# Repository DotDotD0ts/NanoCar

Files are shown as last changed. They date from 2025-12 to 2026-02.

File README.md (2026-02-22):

# NanoCar

Projet pour l'option prototypage de mon école. Je veux créer un petit véhicule électrique (style voiture radiocommandé) avec une carte jetson nano et une caméra pi dans le but de faire de la reconnaissance d'objet pour suivre une cible. La jetson hostera aussi un serveur web contenant un retour caméra ainsi que des controles pour le véhicule.
Le prototype sera développé en Python pour un dévelopement rapide et fonctionnel. 

## To do list

**Management**
- [x] Définition du besoin
- [x] Création du cahier des charges
    - [x] Analyse fonctionnelle
    - [x] Planning prévisionnel
    - [x] Diagramme fast
- [x] Commande du matériel
- [x] WBS (a mettre au propre)
- [x] Mise en place du Gantt
- [x] Budget (a mettre au propre)

**Réalisation physique**
- [x] Réflexion sur la partie direction du véhicule (une bille a l'avant et direction avec un differentiel de rotation dans les roues arrieres)
- [x] Conception 3D
    - [x] Jetson nano
    - [x] LiPo
    - [x] Moteur
    - [x] Driver
    - [x] Camera
    - [x] Regulateur
    - [x] Roue
    - [x] Chassis
    - [x] Roue avant
    - [x] Supports pour l'assemblage
        - [x] Batterie
        - [x] Moteurs
        - [x] Caméra
    - [x] Persage des trous de vis (fixation composants)
    - [x] Assemblage 3D
- [x] Fabrication
- [x] Assemblage
- [x] Branchements

**Réalisation logiciel**
- [x] Setup du wifi de la Jetson Nano (10.42.0.1:3000)
- [x] Ajout d'une connexion ssh pour un accès simple à la Jetson Nano
- [x] Mise en place d'un serveur sur la jetson nano
    - [x] Serveur flask
    - [x] Implémentation des commandes
- [x] Création de l'interface utilisateur
- [x] Mise en place du flux vidéo
- [x] Controle des moteurs
- [x] Control manuel du véhicule
    - [x] Différentiel des moteurs pour la direction
    - [x] Paramétrage de l'accéleration / décéleration
- [x] Intégration d'un modèle open source de reconnaissance d'objet
    - [x] Haar Cascade : reconnaissance de visage (CPU only) très lent, latence de plusieurs secondes + 2-3 FPS max
    - [x] SSD Mobilenet v2 : https://github.com/dusty-nv/jetson-inference, detecte le corps humain (GPU accelerated) latence 1-2 secondes, 60 FPS
- [x] Control autonome du véhicule
- [x] Mode recherche de cible si aucune cible dans le visuel (Ajout d'un boulean pour activer ou non)
- [x] Démarage automatique du serveur (crontab)
- [x] Esquive d'obstacles

**Problèmes**
- [x] Méthode Haar Cascade pour reconaissance de visage trop lente (2-3 fps)
- [x] Support caméra n'a pas d'angle, les visages ne sont reconnu que s'ils sont au niveau du sol

**User experience**
- [x] Syncroniser le slider de speed avec le backend
- [x] Réduire la taille de la cible pour que le robot reste plus loin

**Livrable**
- [x] Création d'un poster de présentation du projet
- [x] Rédaction d'une documentation utilisateur 
- [x] Rédaction d'une documentation technique permettant de refaire le projet de zéro

## Documentations

Cette documentation a été réalisé sur l'outil fabmanager comme demandé par l'école. Pour voir le rendu correct de cette doc, veillez-vous rendre sur [ce lien](https://cesi-fabmanager.duckdns.org/#!/projects/nanocar)

# NanoCar

Illustration

La robotique autonome est le domaine consistant à concevoir  
des systèmes capables d'interagir avec leur environnement. Il  
s’agit d’un point clé avec énormément d’enjeux pour l’industrie  
et la mobilité de demain. L’intelligence artificielle, prenant de  
plus en plus d’importance, permet désormais d'intégrer de la  
vision par ordinateur complexe sur de petits systèmes  
embarqués. C’est pour cela que je vous présente mon robot  
autonome Nanocar. Il a pour but de suivre une personne sans  
intervention extérieur.

Vous pouvez retrouver l’entièreté des fichiers concernant ce projet dans le repo&nbsp;[Github NanoCar](https://github.com/DotDotD0ts/NanoCar)

## Étapes

### Étape 1 : Documentation utilisateur

Dans un premier temps, voici la documentation utilisateur qui vous permettra d'utiliser ce prototype :

1. Branchez la batterie LiPo au connecteur jaune sur le côté du robot. Ce connecteur permet d'alimenter l'entièreté du robot.
2. Vérifiez que la LED du driver clignote en bleu sinon chargez la batterie, cette LED indique que la LiPo est suffisamment chargé pour ne pas perdre en durée de vie. (Le driver est la carte électronique brancher directement à la batterie par le connecteur jaune)
3. Utilisez un appareil pour vous connecter au réseau Wifi NanoCar.
4. Ouvrez un navigateur internet et connectez-vous à l'adresse [http://10.42.0.1:3000/](http://10.42.0.1:3000/.)&nbsp;. Cela vous permettra d'avoir l'accès à la page de contrôle du robot.

Utilisation du robot à partir de la page de contrôle :

- Utilisez les flèches directionnelles sur l'écran de contrôle ou sur votre clavier pour faire bouger le robot. (La touche espace permet de freiner)
- Changez la vitesse du robot à l'aide du slider en dessous des boutons.
- Le bouton MODE permet de changer entre les 2 modes du robot : le mode manuel (par défaut) où vous contrôlez le robot à l'aide de l'interface et le mode automatique où une IA va prendre le contrôle du robot est va essayer de suivre une personne. Dans le mode automatique, vous remarquerez que le retour caméra affiche des informations sur ce que l'IA reconnais.&nbsp;
- Le bouton SEARCH permet, en mode automatique, au robot de chercher sa cible au lieu d'attendre qu'elle passe dans son champ de vision.

Enfin pour éteindre le robot il suffit de débrancher le connecteur jaune de la batterie.



### Étape 2 : La liste de course

Pour ce projet, j'ai réutilisé un maximum de composants d'autres projets du Fablab, vous n'êtes en aucun cas obligé de réutiliser les mêmes références. La seul nécessité est que le driver des moteurs accepte une communication série bien particulière. Il reste possible d'adapter le code pour la communication entre la Jetson Nano et le driver.

Voici les composants / matériaux utilisés :

- Une planche de bois de 6mm d'épaisseur.
- 42g de PLA.
- Une multitude de petit câble mâle vers mâle et femelle vers mâle.
- Une multitude de vis et d'écrou m2 et m3
- 2 roues avec une vis permettant de sécuriser la roue à l'axe du moteur.
- 1 ball caster pour la roue avant.
- 2 moteurs DC. Ici des&nbsp;[313 RPM HD Premium Planetary Gear Motor w/Encoder](https://www.servocity.com/313-rpm-hd-premium-planetary-gear-motor-w-encoder/). Ils sont beaucoup trop puissant par rapport aux attentes du prototype.
- Un driver pour contrôler les moteurs. Ici une Sabertooth 2x25. De même pas besoin d'un contrôleur aussi poussé. Si vous ne souhaitez pas toucher au code, il vous faudra un driver qui peut être contrôlé par une communication série de la même façon que la Sabertooth. (Vérifiez que la partie simplified serial de la documentation de votre driver corresponde à la&nbsp;[documentation Sabertooth](https://www.dimensionengineering.com/datasheets/Sabertooth2x25.pdf)). Sinon vous pouvez toujours adapter le fichier command.py pour que la communication corresponde à votre driver.
- Une Jetson Nano (le cerveau du robot qui permet de faire tourner un modèle de reconnaissance d'objet).
- Une carte micro SD de 32Go.
- Une caméra Pi camera v2.1. Dans le cas où vous voulez en utiliser une autre il faudra modifier l'initialisation de la caméra dans le fichier camera.py pour que la librairie OpenCV puisse récupérer l'image.
- Un&nbsp;[dongle Wifi](https://www.amazon.fr/Cudy-Adaptateur-WU300-Hotspot-compatible/dp/B0FR443YP5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) qui fait Access point et qui fonctionne sur Linux. Vérifiez bien les 2 mentions à l'achat.
- Une batterie LiPo 4S.
- Un connecteur XT60 femelle pour connecter le driver à la LiPo.
- Un régulateur de courant pour faire descendre le 14V de la batterie en 5V pour l'alimentation de la Jetson Nano.
- Un cable d'alimentation 5V 4A pour alimenter la Jetson Nano.
- Dans le cas où votre driver est contrôlé par du 5V comme sur la Sabertooth, il vous faudra un level shifter 3V vers 5V pour éviter de cramer la Jetson Nano. Il est nécessaire de protéger la Jetson Nano qui ne prend que du 3V sur les pins I/O.

### Étape 3 : Préparation de la Jetson Nano

Maintenant que nous avons tous les composants, commençons la réalisation.

Brancher le dongle Wifi sur la Jetson Nano ainsi que la carte micro SD et la caméra.

Dans un premier temps, il vous faudra installer l'OS sur la Jetson Nano. Pour cela, je vous laisse suivre le guide fourni par Nvidia : [https://developer.nvidia.com/embedded/learn/get-started-jetson-nano-devkit](https://developer.nvidia.com/embedded/learn/get-started-jetson-nano-devkit). Je vous conseille de définir le nom d'utilisateur en tant que 'nano' vu que c'est celui qui sera utiliser pour le reste de la documentation.

Pour la suite, il va être important d'être connecter à internet. Pour cela, utilisez l'utilitaire graphique d'Ubuntu en haut à droite de l'écran ou nmtui si vous utilisez une connexion serial ou ssh à la carte.

Une fois connecté à un réseau Wifi ayant un accès internet, à l'aide d'un terminal, exécuter les commandes suivantes :

Mettre en place le DNS :

    sudo echo "nameserver 8.8.8.8" > /etc/resolv.conf
    sudo systemctl restart NetworkManager

Installer les dépendances :

    sudo apt-get update
    sudo apt-get install python3-pip cmake git  
    pip3 install flask libpython3-dev python3-numpy

Pour préparer git pour récupérer le code source du projet ainsi que celui des dépendances. Vous pouvez mettre ce que vous souhaitez en nom utilisateur et email :&nbsp;

    git config --global user.name "[votre nom d'utilisateur]"
    git config --global user.email "[votre email]"

Installer Jetson Inference est nécessaire pour la partie reconnaissance d'objet du projet :

    sudo apt-get install git cmake libpython3-dev python3-numpy
    git clone --recursive --depth=1 https://github.com/dusty-nv/jetson-inference
    cd jetson-inference
    mkdir build
    cd build
    cmake ../
    make -j$(nproc)
    sudo make install
    sudo ldconfig

Voici le lien de la documentation d'où viennent les commandes : [https://github.com/dusty-nv/jetson-inference/blob/master/docs/building-repo-2.md](https://github.com/dusty-nv/jetson-inference/blob/master/docs/building-repo-2.md).

Ensuite, copier le répertoire Github de NanoCar avec la commande :

    git clone[https://github.com/DotDotD0ts/NanoCar.git](https://github.com/DotDotD0ts/NanoCar.git)

Enfin, pour que le code se lance à chaque démarrage, nous allons configurer l'utilitaire linux crontab :

    sudo crontab -e

Cette commande va vous ouvrir un fichier dans lequel il va falloir mettre la ligne suivante :&nbsp;

    @reboot python3 /home/nano/NanoCar/src/main.py

Sauvegardez le fichier avec Ctrl + o puis fermez le avec Ctrl + x.

Maintenant, plus besoin de connexion internet, nous pouvons préparer la carte à créer son propre réseau Wifi pour si connecter.

Pour cela, ouvrez un terminal puis entrez les commandes suivantes :

    # 1. Création de la connexion et du nom du réseau (SSID = NanoCar)sudo nmcli con addtypewifi ifname wlan0 con-name NanoCar autoconnect yes ssid NanoCar# 2. Force le mode Point d'Accèssudo nmcli con modify NanoCar 802-11-wireless.mode ap# 4. Configuration IP (Serveur DHCP)sudo nmcli con modify NanoCar ipv4.method shared# 5. Force la bande 2.4GHz (Plus stable)sudo nmcli con modify NanoCar 802-11-wireless.bandbg  
      
    # 6. Rendre l'adresse IP statique  
    sudo nmcli con modify NanoCarHotspot ipv4.addresses 10.42.0.1/24
      
    # 7. Activer l'interface  
    sudo nmcli con up NanoCar

Maintenant, il est possible de se connecter à la carte avec un ordinateur. Pour cela, connectez l'ordinateur au réseau Wifi NanoCar puis ouvrez un terminal et connectez-vous en SSH :

    ssh nano@10.42.0.1

Le mot de passe du compte utilisateur vous sera demandé.

Cette connexion SSH vous permettra de faire des modifications au code source en cas de besoin.

### Étape 4 : Fabrication

Prenez votre planche en bois, une découpeuse laser et utilisez le CAD du châssis (retrouvable sur le Github dans le dossier CAD) ou le pdf pour découper le châssis dans la planche en bois. Vous pouvez aussi graver les emplacements des différents composants pour rendre l'assemblage plus simple.

Imprimez les supports en PLA à partir des modèles 3D. (vous retrouverez aussi les CAD dans le Github).

Prenez un crayons fin et long puis placez les différents composants, supports imprimés et le ball caster sur la planche en bois. Vous pouvez ainsi marquer les trous à faire pour les vis. Pour placer les composants, référez-vous au CAD NanoCar assemblage ou à l'image de la réalisation finale.

Avec votre châssis marqué, utilisez la perceuse à colonne pour faire des trous de 2 et 3 mm de diamètre. L'image ci-dessus vous permettra de savoir quelles trous doivent être de quelle diamètre.

Il va falloir régler le régulateur de courant, pour cela équipez-vous d'un petit tournevis plat, d'une alimentation 14V (vous pouvez utilisez la batterie directement) et d'un multimètre. Branchez l'alimentation au borne IN + et - du régulateur, réglez votre multimètre en mode voltmètre 20V en courant continu, poser les bornes de votre multimètre sur la sortie OUT + et - puis tourner le potentiomètre bleu à l'aide du tournevis plat jusqu'à ce que vous lisiez 5V sur le multimètre. Cette étape est extrêmement importante pour ne pas griller la Jetson Nano.

Sur la Sabertooth 2x25, vous allez retrouver 6 switchs qui permettent de configurer le driver, je vous laisse lire la&nbsp;[documentation officielle](https://www.dimensionengineering.com/datasheets/Sabertooth2x25.pdf)&nbsp;pour comprendre ce que la configuration suivante fait :&nbsp;

1. ON : Sélection du mode
2. OFF : Sélection du mode
3. ON : Option de protection de la batterie Lithium
4. OFF : Sélection du baud rate
5. ON&nbsp;: Sélection du baud rate
6. ON : Sélection du mode simple serial

Maintenant pour la dernière étape avant l'assemblage final, il va vous falloir souder 6 files sur le level shifter. Du côté LV, il vous faudra des mâles vers femelles et du côté HV il vous faudra des mâles vers mâles.





### Étape 5 : Assemblage

Voici maintenant les étapes de l'assemblage. Vous retrouverez dans les images un schéma électroniques ainsi que toutes les étapes de l'assemblage dans l'ordre.

Vu qu'aucun pas de vis n'est mis en place, nous utiliserons une vis ainsi qu'un écrou pour serrer à chaque fois que j'indique "Vissez".

1. Vissez le régulateur de courant sur le châssis.
2. Connectez le câble d'alimentation 5V pour la Jetson Nano en sortie (le rouge sur le OUT+ et le noir sur le OUT-) et 2 files mâles vers mâles en entrée.
3. Vissez la Jetson Nano.
4. Connectez le driver au level shifter, 5V -\> HV, 0V -\> GND côté HV et le S1 -\> HV1. Vissez le driver.
5. Vissez les supports moteurs sans les serrer puis placer les moteurs. Enfin, serrer les supports pour que les moteurs ne puissent pas bouger. Vissez les supports de la batterie à l'avant.
6. Vissez le support caméra, ne le serré pas trop fort, la batterie viendra aligner la caméra.
7. Branchez le câble d'alimentation 5V à la Jetson Nano. Branchez le connecteur XT60 femelle ainsi que le régulateur de courant au driver, rouge -\> B+ et noir -\> B- ainsi que IN+ -\> B+ et IN- -\> B-. Branchez le level shifer à la JetsonNano, LV -\> 3.3V, GND -\> GND, LV1 -\> pin 8.
8. Branchez les moteurs au driver, Moteur B (à gauche sur l'image) : rouge -\> MB+, noir -\> MB-, Moteur A (à droite sur l'image) : rouge -\> MA+, noir -\> MA-. Vissez les roues sur les moteurs arrière et le ball caster à l'avant.
9. Glissez la batterie dans son emplacement avec le connecteur vers le driver. Enfin, connectez le connecteur jaune XT60 femelle au connecteur de la batterie. Une LED bleu devrait clignoter sur le driver, une LED rouge devrait s'allumer sur le régulateur de courant ainsi que sur la Jetson Nano.

Vous devriez maintenant vous retrouver avec un prototype fonctionnel.





















### Étape 6 : Programmation

Avec ce prototype enfin fonctionnel, il est temps de rentrer dans les détails de la logique. Si vous souhaitez modifier le code source, connectez-vous à l'aide de la connexion SSH comme expliqué à la fin de l'étape 3. Dans le cas où vous n'arrivez pas à vous connecter par le Wifi du robot, il reste possible de brancher directement un câble Ethernet entre le robot et votre PC puis de se connecter en SSH par l'ip de cette connexion.

Pour votre information, les technologies suivantes sont indispensable à ce projet :

- Jetson inference plus précisément SSD-Mobilnet-V2 qui est le modèle d'IA utilisé
- OpenCV une librairie très connu pour son efficacité dans le traitement d'image, ici utilisé pour récupérer le flux vidéo de la caméra
- Flask une libraire permettant de mettre en place très facilement un serveur web
- Enfin, pour la simplicité du langage et la rapidité d'écriture, tout le code est écris en python&nbsp;

Vous retrouverez tous les fichiers dans le dossier src du projet Github.

* * *

**Mise en place du serveur web (voir le fichier main.py)**

Vous pouvez retrouver le point d'entré de ce programme qui lance tout simplement le serveur web.&nbsp;

Dans ce fichier, nous retrouvons aussi la définition des routes du serveur web :

- La route par défaut /, amène sur l'écran de contrôle
- La route /videoFeed, envoie le flux caméra depuis le serveur
- La route /command, permet d'envoyer des commandes au serveur
- La route /currentSpeed, permet la synchronisation de la vitesse entre l'affichage et la vitesse réel du robot&nbsp;

Si vous souhaitez modifier l'écran de contrôle, vous retrouverez le fichier home.html dans le dossier page.

* * *

**Contrôle du véhicule (voir le fichier command.py)**

Dans ce fichier il y a la définition du pin de contrôle de la Jetson Nano avec la variable driverPin, ainsi que l'ouverture de la communication série entre la Jetson et le driver. Le serial port est définit dans la data sheet de la Jetson Nano et le baud rate doit correspondre à la configuration du driver.

La fonction driveMotor permet de transformer une simple vitesse avec un id de moteur en instruction compréhensible par le driver.

Enfin, la fonction execCommand recense toutes les commandes que le serveur peut recevoir et exécute le code permettant d'effectuer cette commande.

* * *

**Un accès simple à des valeurs (voir fichier globalVar.py)**

Pour transmettre facilement une valeur entre des fichiers python, la solution la plus simple reste d'avoir un fichier qui contient les variables à partager en tant que variable globale et d'importer ce fichier.

* * *

**IA et caméra (voir le fichier camera.py)**

Ce fichier rassemble la récupération du flux caméra ainsi que l'exécution de l'IA avec un post traitement pour afficher ce que l'IA a reconnue.

Dans un premier temps, nous ouvrons un chemin entre notre programme est la caméra à l'aide d'OpenCV que l'on va appeler un stream. Cette partie d'initialisation se fait à l'aide d'une chaîne de caractère très particulière qui indique à la Jetson Nano la qualité de l'image, le format de celle-ci ainsi que la fréquence d'image. Ici notre caméra peut se permettre de filmer dans une multitude de qualité dont de la 4k, mais pour notre utilisation, nous préférons la qualité la plus basse soit de la HD mais avec une fréquence d'image bien plus importante. Cela permet à l'IA de prendre beaucoup moins de temps à trouver sa cible et aussi à la suivre de façon plus précise.

Nous retrouvons ensuite l'initialisation du modèle d'IA SSD-Mobilnet-V2 avec un threshold définit ici à 60%. Ce threshold correspond à la confiance du modèle IA dans la reconnaissance d'un objet. Ce paramètre permet de contrôler les faux positifs. Si vous avez beaucoup de faux positif, augmentez le threshold sinon dans le cas contraire où le modèle ne reconnais pas de cible, baisser le.

Puis viennent quelques configuration :

- FRAME\_WIDTH correspond à la largeur du retour caméra définit plus haut.
- DEAD\_ZONE\_X correspond aux nombres de pixels autour du centre qui vont être considéré comme le centre. Cela évite que le robot oscille quand il essaie de pointer vers une cible.
- TARGET\_AREA correspond aux nombres de pixels chercher par le robot pour s’arrêter. Cela va contrôler la distance d'arrêt du robot par rapport à la cible. Si le robot se rapproche trop, réduisez ce nombre, sinon s'il s'éloigne trop, augmentez ce nombre.
- AREA\_TOLERANCE correspond aux nombres de pixels autour de la TARGET\_AREA qui vont être considéré comme la cible. Similairement à la variable DEAD\_ZONE\_X, cela permet d'éviter que le robot oscille d'avant en arrière lorsqu'il est à distance d'arrêt de la cible.&nbsp;&nbsp;

La fonction generateFrames est la fonction qui va permettre au serveur web d'envoyé le flux vidéo à l'écran de contrôle.

Enfin la fonction followTarget permet de passer l'image à l'IA qui nous donne une liste d'objets détectés ainsi que leur position. Nous cherchons dans cette liste la cible définit par globalVar.target\_class\_id (ici 1, si vous souhaitez que la cible soit autre chose qu'un humain, je vous laisse chercher le class id correspondant dans la&nbsp;[documentation du modèle](https://github.com/dusty-nv/jetson-inference/blob/master/data/networks/ssd_coco_labels.txt) est le remplacer). En priorité nous essayons d'esquiver l'obstacle le plus proche s'il est plus proche que la cible. Puis nous allons dans la direction de la cible. Pour finir, nous mettons à jour l'image du flux vidéo en y dessinant un rectangle vert pour la cible et des rectangles rouges pour les obstacles ainsi que leur catégorie

### Étape 7 : Conclusion

Dans l'ensemble, ce prototype est sorti comme imaginer au début du projet. Il correspond au CAD réalisé, toutes les fonctionnalités du cahier des charges sont présentes enfin la réalisation a pris moins de temps que prévu.

Le seul problème rencontré est la remonté d'un courant 5V par l'input S1 du driver dans le pin 8 (3,3V) de la Jetson Nano, ce qui a brulé un composant de celle-ci. Une solution simple a était trouvé rapidement avec l'ajout d'un level shifter.

Malgré un prototype fonctionnel de multiples améliorations sont possibles. Voici une liste non exhaustive d'idées pour améliorer ce prototype :

- Améliorer la logique d'esquive d'obstacles
- Ajouter une sélection de la cible
- Réduire la latence en mode automatique
- Revoir les contrôles du véhicules (par exemple une fonction lerp) pour rendre les contrôles moins brute, plus réalistes (accélération / décélération)
- Permettre à l'IA de faire plusieurs actions à la fois (tourner et avancer en même temps)
- Créer une petite dance de la victoire une fois que le robot à atteint sa cible

Avec cette documentation technique, vous pouvez maintenant modifié ce robot pour lui ajouter d'autres fonctionnalités que ce soit logiciel (enregistrement du flux vidéo) ou électronique (ajout d'un bras robotisé). Ce prototype a pour objectif final de servir de base pour réaliser des projets plus complexes avec plus de temps.

## Auteur

Nicolas Ridoire

## Thématiques

Robotique, Prototypage

## Fichiers CAD

support_moteur.stl

support_camera.stl

Support_batterie.stl

pdf_chassi.pdf

## Statut

Terminé

## Machines utilisées

Découpeuse laser, Bambu Lab H2S

## Matériaux utilisés

Bois Contre plaqué, Filament PLA

## Licence

Attribution + Pas d'Utilisation Commerciale (BY NC)

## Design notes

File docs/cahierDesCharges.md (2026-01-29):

# Cahier des charges

## Sommaire

1. Contexte et objectifs du projet
2. Description fonctionnelle
3. Spécifications techniques
4. Contraintes du projet
5. Critères de validation
6. Planning prévisionnel
7. Documents annexes

## 1. Contexte et objectifs du projet

Ce projet rentre dans l'option prototypage qui demande une réalisation comprenant modélisation 3D et programmation.
Le projet NanoCar doit permettre à un utilisateur de suivre une personne à distance à l'aide d'un véhicule motorisé.
L'objectif est de concevoir et réaliser un véhicule automatique pouvant suivre une personne. Ce véhicule devra être controlable par une interface web en mode automatique ou manuel avec un retour vidéo.

## 2. Description fonctionnelle

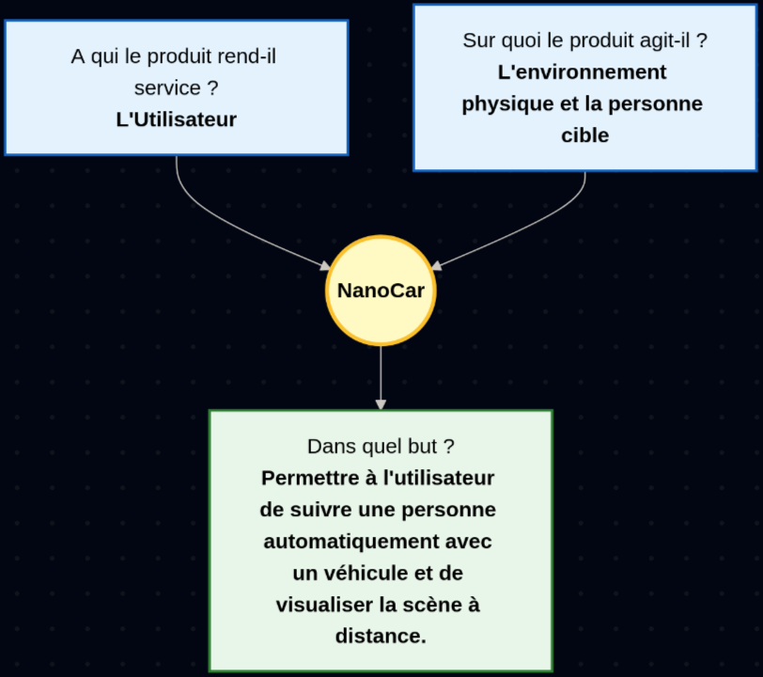
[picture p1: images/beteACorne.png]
Bête à corne


Fonction principal: Permettre à l'utilisateur de visualiser et de suivre automatiquement une cible.
Fonction secondaires: 
- Contrôle du véhicule à distance en mode manuel
- Enregistrer le flux vidéo

L'utilisateur cherche à suivre une cible à distance de manière automatisé.
L'utilisateur cherche à se filmer de manière automatisé.

L'interface devra être accessible sur le web pour éviter toutes installations à l'utilisateur. De préférence, cette interface sera responsive pour qu'elle puisse être utilisé sur n'importe quel device ayant accès à internet.

## 3. Spécifications techniques

Matériel:
|Nom|Référence|Quantité|
|-|-|-|
|Motor driver|sabertooth 2x25|1|
|DC motor|313 RPM HD Premium Planetary Gear Motor w/Encoder|2|
|Lipo battery|4s, 13.4V 4200mAh|1|
|Régulateur de courant|DFR0946|1|
|Planche en bois pour le chassis| |1|
|Roues| |3|
|Jetson Nano|Jetson Nano 4Gb|1|
|Raspberry Pi Camera|Pi Camera V2.1|1|
|USB Wifi Dongle| Clé Wi-Fi USB 2.0 RF Solutions, 802.11b, 802.11g, 802.11n|1|

Le véhicule devra pouvoir suivre une cible pendant au moins 5 minutes à une vitesse de 5 km/h (vitesse moyenne de marche d'un humain), il devra pouvoir éviter les obstacles et retrouver sa cible.

## 4. Contraintes du projet

Le projet est financé par le CESI avec un budget maximum de 150 eur. Certains des matériaux (comme la caméra pi, les roues, le bois, ...) sont déjà présent au CESI. La carte Jetson Nano sera fourni par mes soins et récupéré à la fin du projet.

Dans un premier temps, le chassis du véhicule sera fait à partir d'une planche en bois découpé à l'aide de la découpeuse laser.

Les commandes devront être effectué avant le mercredi 17 décembre pour prendre en compte le temps de traitement et de livraison de celles-ci.
Enfin, le projet devra être rendu le 30 janvier 2026, jour de la soutenance.
Un rapport contenant le cahier des charges ainsi qu'une documentation technique et utilisateur devra être rendu à la même date.

## 5. Critères de validation

Pour assurer le bon respect de ce cahier des charges, les tests suivants devront être validé :
- Le véhicule se déplace au moins à 3km/h
- Le véhicule peut se déplacer pendant au moins 5 minutes
- Le véhicule peut suivre une cible malgrès des obstacles sur son chemin
- Le véhicule doit être mise en fonctionnement par une personne ayant le manuel utilisateur
- Le véhicule doit être contrôlable en mode manuel par une personne non formé
- Le flux vidéo est fluide (>24.99 fps)

Pour suivre l'avancement du projet, plusieurs KPI peuvent être mis en place :
- Utilisation du budget (budget dépensé / budget total)
- Pourcentage des tâches du WBS terminées
- Nombres de systèmes individuels validés

Enfin, pour valider le projet, les indicateurs suivants seront utilisés :
- Latence <300ms entre le flux vidéos et la réalité
- Durée de fonctionnement >5min
- Vitesse >3km/h
- Un utilisateur qui n'a jamais utilisé le projet peut le mettre en fonctionnement en <10min

## 6. Planning prévisionnel

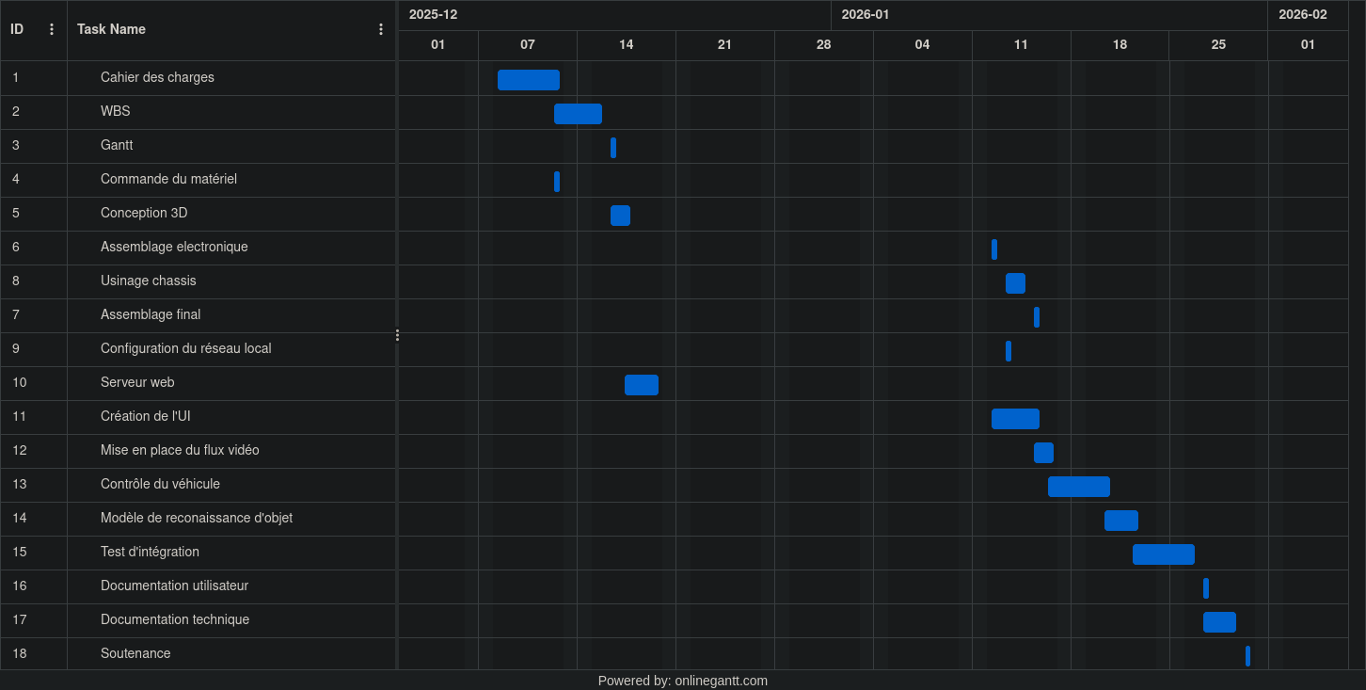
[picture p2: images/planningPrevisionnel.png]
Planning prévisionnel


Les deadlines importantes sont :
- 17/12/2025: Fin des premières commandes
- 16/01/2026: Assemblage final
- 21/01/2026: Tests d'intégration
- 30/01/2026: Soutenance final

## 7. Documents annexes

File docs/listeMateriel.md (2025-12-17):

# Liste matériel

|ID|Nom|Référence|Prix unitaire|Quantité|Prix total|
|---|---|----|---|---|---|
|1|Motor driver|Sabertooth 2x25|125 eur|1|125 eur|
|2|DC motor|313 RPM HD Premium Planetary Gear Motor w/Encoder|60 eur|2|120 eur|
|3|Lipo battery|4s, 13.4V 4200mAh |33 eur|1|33 eur|
|4|Régulateur de courant|DFR0946|10.70 eur|1|10.70 eur|
|5|Jetson Nano|Jetson Nano 4Gb|250 eur|1|250 eur|
|6|Raspberry Pi Camera|Pi camera v2.1|15 eur|1|15 eur|
|7|Wifi dongle|Clé Wi-Fi USB 2.0 RF Solutions, 802.11b, 802.11g, 802.11n|12.55 eur|1|12.55 eur|
|8|Câble d'alimentation 5V4A| | |1| |
|9|Connecteurs de batterie LiPo|Connecteur male + femelle| |1| |
| |Total| | | | |

Liens : 
4. https://www.gotronic.fr/art-regulateur-1-a-33-vcc-dfr0946-35165.htm
7. https://www.conrad.fr/fr/p/adaptateur-wi-fi-tp-link-archer-t2u-nano-usb-2-0-600-mbit-s-1898621.html

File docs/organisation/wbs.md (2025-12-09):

```mermaid

graph 
    %% Projet Racine
    Projet[<b>NanoCar</b>]

    %% Niveau 1 : Les grands lots
    Lot1[1. Conception & Gestion]
    Lot2[2. Hardware & Mécanique]
    Lot3[3. Développement Logiciel]
    Lot4[4. Intégration & Tests]

    %% Liens Niveau 1
    Projet --> Lot1
    Projet --> Lot2
    Projet --> Lot3
    Projet --> Lot4

    %% Niveau 2 : Détails Lot 1
    Lot1 --> L1T1[Définition du cahier des charges]
    Lot1 --> L1T2[Choix des composants <br/>BOM]
    Lot1 --> L1T3[Conception 3D des supports]

    %% Niveau 2 : Détails Lot 2
    Lot2 --> L2T1[Montage du châssis]
    Lot2 --> L2T2[Fixation Jetson & Caméra]
    Lot2 --> L2T3[Installation des moteurs]

    %% Niveau 2 : Détails Lot 3
    Lot3 --> L3T1[Installation OS]
    Lot3 --> L3T2[Dev: Serveur Web]
    Lot3 --> L3T3[Dev: Pilotage Moteurs]
    Lot3 --> L3T4[Dev: IA & Tracking]

    %% Niveau 2 : Détails Lot 4
    Lot4 --> L4T1[Tests unitaires]
    Lot4 --> L4T2[Calibration du Tracking]
    Lot4 --> L4T3[Démonstration finale]

    %% Styles
    style Projet fill:#212121,stroke:#000,stroke-width:2px,color:#fff
    style Lot1 fill:#BBDEFB,stroke:#1976D2,color:#000
    style Lot2 fill:#C8E6C9,stroke:#388E3C,color:#000
    style Lot3 fill:#FFF9C4,stroke:#FBC02D,color:#000
    style Lot4 fill:#E1BEE7,stroke:#8E24AA,color:#000
```

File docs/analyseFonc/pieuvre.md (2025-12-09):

- FP1: Permettre à l'utilisateur de visualiser et de suivre automatiquement une cible.
- FC1: Être autonome en énergie pour alimenter la Jetson et les moteurs.
- FC2: Se déplacer sur le sol sans glisser et franchir de petits obstacles.
- FC3: Transmettre les données et recevoir les commandes via Wi-Fi (Serveur Web).

```mermaid
graph 
    %% Le Système central
    System((<b>NanoCar</b>))

    %% Les Éléments extérieurs
    Utilisateur[Utilisateur / Opérateur]
    Cible[Personne Cible]
    Sol[Sol / Environnement]
    Energie[Énergie / Batterie]
    Reseau[Réseau / Interface Web]

    %% Relations pour les Fonctions Principales (FP)
    Utilisateur -- <b>FP1</b> --- System
    Cible -- <b>FP1</b> --- System

    %% Relations pour les Fonctions Contraintes (FC)
    Energie -- <b>FC1</b> --- System
    Sol -- <b>FC2</b> --- System
    Reseau -- <b>FC3</b> --- System

    %% Styles pour la lisibilité
    style System fill:#FFF9C4,stroke:#FBC02D,stroke-width:4px,color:#000
    style Utilisateur fill:#E1F5FE,stroke:#0288D1,color:#000
    style Cible fill:#E1F5FE,stroke:#0288D1,color:#000
    style Sol fill:#EEEEEE,stroke:#9E9E9E,color:#000
    style Energie fill:#FFEBEE,stroke:#D32F2F,color:#000
    style Reseau fill:#E8F5E9,stroke:#388E3C,color:#000
```

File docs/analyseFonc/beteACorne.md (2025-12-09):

```mermaid
graph
    %% Définition des nœuds
    User[A qui le produit rend-il service ?<br/><b>L'Utilisateur / Opérateur</b>]
    Target[Sur quoi le produit agit-il ?<br/><b>L'environnement physique et la personne cible</b>]
    Product((<b>NanoCar</b>))
    Function[Dans quel but ?<br/><b>Permettre à l'utilisateur de suivre une personne automatiquement avec un véhicule et de visualiser la scène à distance.</b>]

    %% Définition des liens
    User --> Product
    Target --> Product
    Product --> Function 

    %% Styles pour ressembler à un bête à cornes classique
    style User fill:#E3F2FD,stroke:#1565C0,stroke-width:2px,rx:10,ry:10,color:#000
    style Target fill:#E3F2FD,stroke:#1565C0,stroke-width:2px,rx:10,ry:10,color:#000
    style Product fill:#FFF9C4,stroke:#FBC02D,stroke-width:3px,color:#000,font-size:16px
    style Function fill:#E8F5E9,stroke:#2E7D32,stroke-width:2px,rx:20,ry:20,color:#000
```

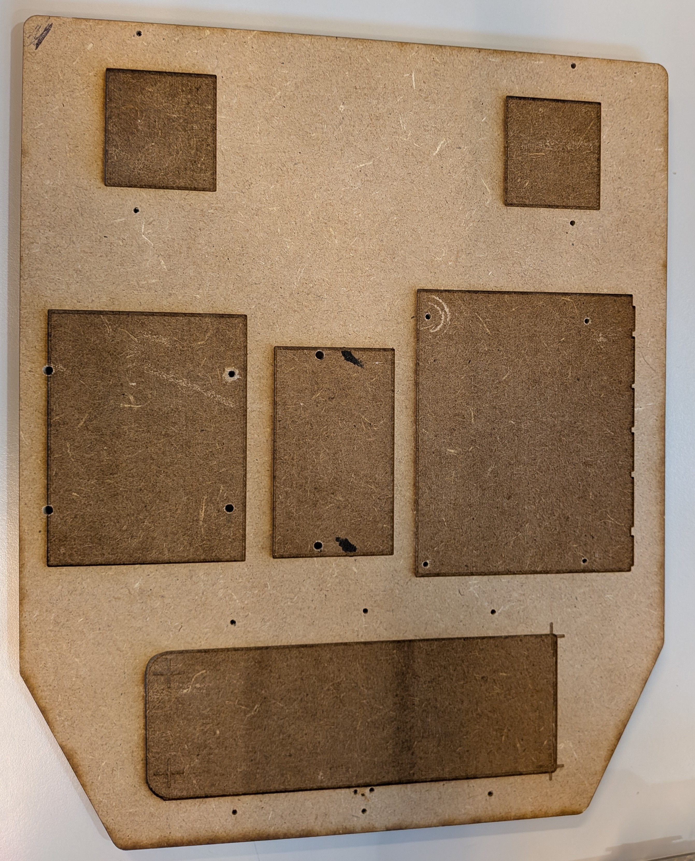
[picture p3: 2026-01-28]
images/Montage/chassis.jpg

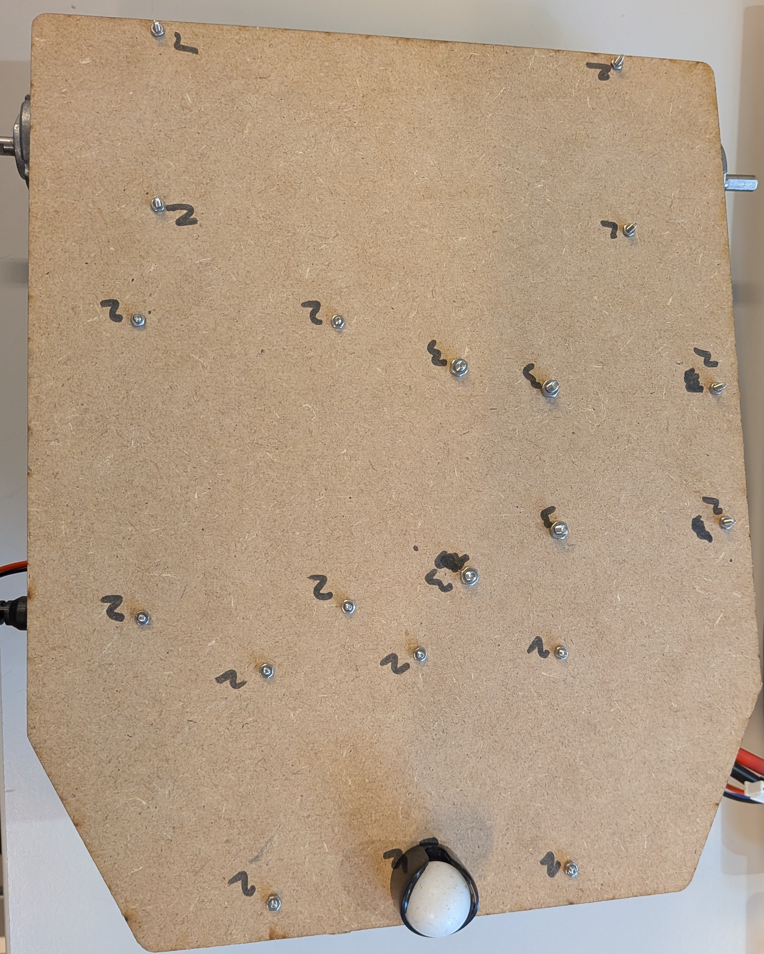
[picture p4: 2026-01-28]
images/Montage/dessous chassis.jpg

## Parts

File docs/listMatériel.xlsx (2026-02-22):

Nom | Lien | Prix (eur) | Quantité | Total (eur)
Controller de moteurs | https://www.gotronic.fr/art-commande-sabertooth-2x25a-11575.htm | 124.9 | 1 | 124.9
Moteurs | https://www.servocity.com/313-rpm-hd-premium-planetary-gear-motor-w-encoder/ | 50.25 | 2 | 100.5
Batterie LiPo | https://www.amazon.fr/-/en/Rechargeable-Connectors-Airplane-Helicopter-Quadcopter/dp/B0DM8WMH1B | 41.99 | 1 | 41.99
Régulateur de courant | https://www.gotronic.fr/art-regulateur-1-a-33-vcc-dfr0946-35165.htm | 10.7 | 1 | 10.7
Jetson Nano | https://www.gotronic.fr/art-jetson-nano-developer-kit-waveshare-35844.htm | 249 | 1 | 249
Raspberry Camera v2 | https://www.gotronic.fr/art-camera-officielle-8-mpx-rb-cam-v2-26774.htm | 19.9 | 1 | 19.9
Dongle WiFi | https://www.amazon.fr/Cudy-Adaptateur-WU300-Hotspot-compatible/dp/B0FR443YP5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 | 6.9 | 1 | 6.9
Convertisseur logique | https://www.gotronic.fr/art-convertisseur-de-4-niveaux-logiques-21529.htm | 3.95 | 1 | 3.95
Planche en bois |  | 15.14 eur/m2 | 0.057585 m2 | 0.8718369 | 15.14 | 0.057585
PLA |  | 22.99 eur/kg | 41.47 g | 0.55
Humain |  | 21 eur/h | 135 h | 2835
Total |  |  |  | 3394.261837
Total sans humain |  |  |  | 559.2618369
Total payé |  |  |  | 291.8718369

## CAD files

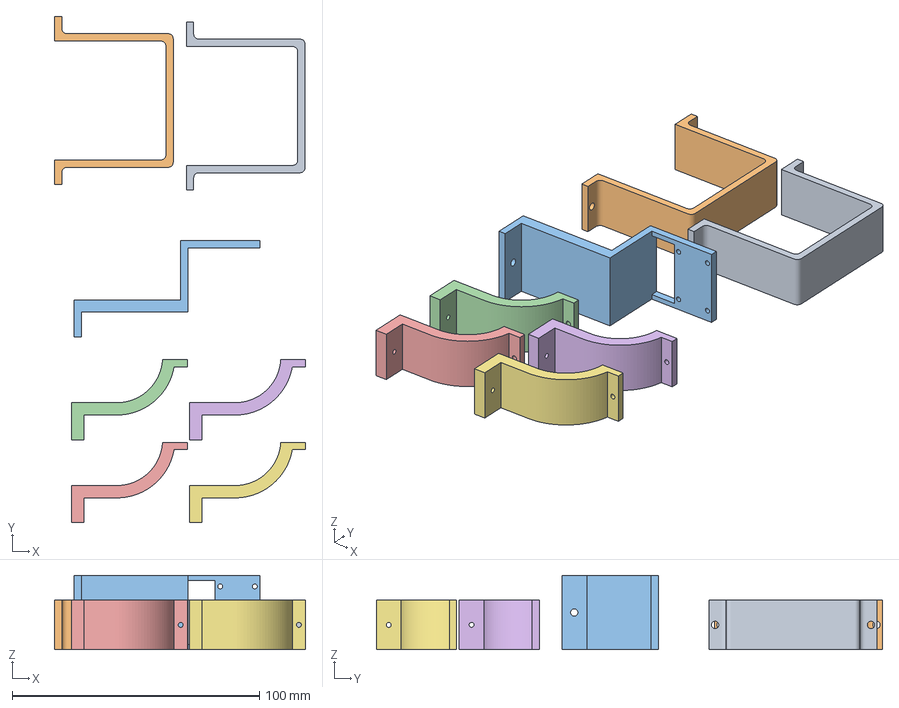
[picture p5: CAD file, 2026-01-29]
CAD/Support batterie.3mf
101.4 x 204.6 x 30.0 mm
Support batterie.stl x 2
support camera.stl
support moteur.stl x 4

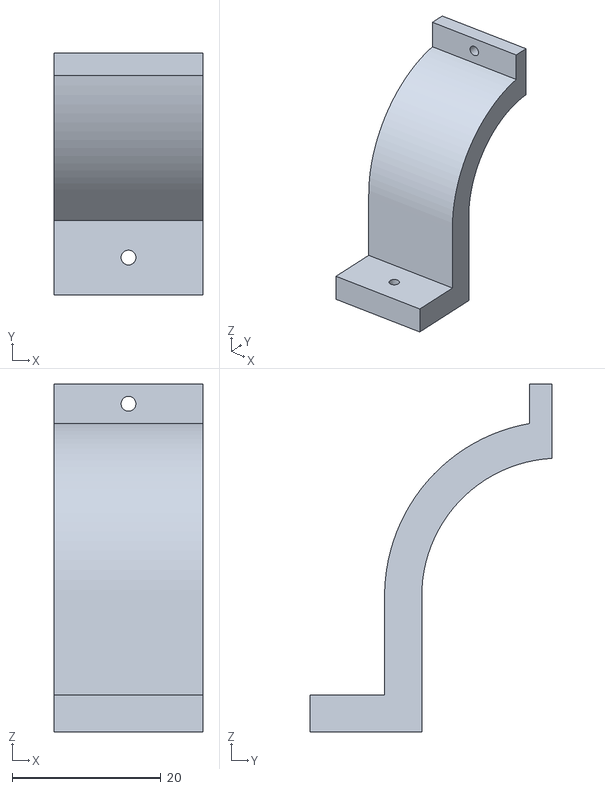
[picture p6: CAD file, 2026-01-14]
CAD/support moteur.stl
20.0 x 32.5 x 46.8

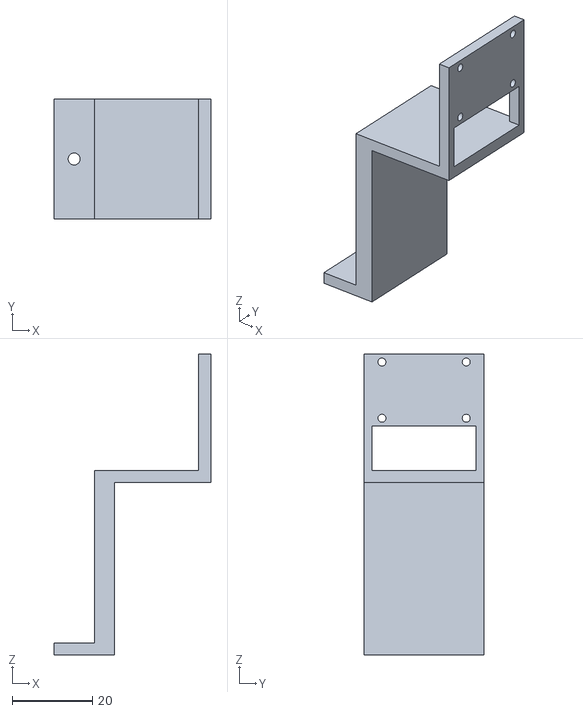
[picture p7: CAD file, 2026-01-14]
CAD/support camera.stl
39.0 x 30.0 x 75.0

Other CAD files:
CAD/Camera.f3d
CAD/Jetson nano.f3d
CAD/Moteur.f3d
CAD/Nanocar assemblage.f3z
CAD/Regulateur de tension.f3d
CAD/Support batterie.stl
CAD/batterie.f3d
CAD/chassis.f3d
CAD/driver.f3d
CAD/roue avant.f3d
CAD/roue.f3d

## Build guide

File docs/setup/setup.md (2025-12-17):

# Guide de setup

## Jetson Nano

1. Pour le setup de base (installation de l'OS et configuration), suivre la documentation officiel Nvidia : https://developer.nvidia.com/embedded/learn/get-started-jetson-nano-devkit
2. Pour pouvoir développer localement, l'utilisation d'une connexion ssh et la méthode la plus simple. Pour cela, connecter votre pc à la Jetson Nano via un câble ethernet et paramétrer les interfaces de chaque appareil de façon statique pour simplifier la communication.
```bash
sudo iptables -t nat -A POSTROUTING -o wlan0 -j MASQUERADE
sudo iptables -A FORWARD -i enp4s0 -o wlan0 -j ACCEPT
sudo iptables -A FORWARD -i wlan0 -o enp4s0 -m state --state RELATED,ESTABLISHED -j ACCEPT
```
3. Ajouter les dns suivant pour avoir une résolution de nom qui fonctionne sur la Jetson Nano dans le fichier /etc/resolve.conf:
```
namespace 10.42.0.1
namespace 8.8.8.8
namespace 8.8.8.4
```
4. Pour tester le code sur la carte, utiliser git pour mettre à jour le repo

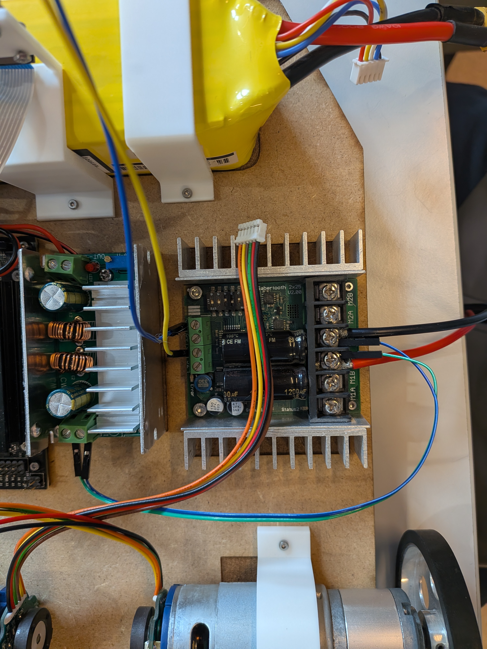
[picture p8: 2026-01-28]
images/Montage/alimentation driver.jpg

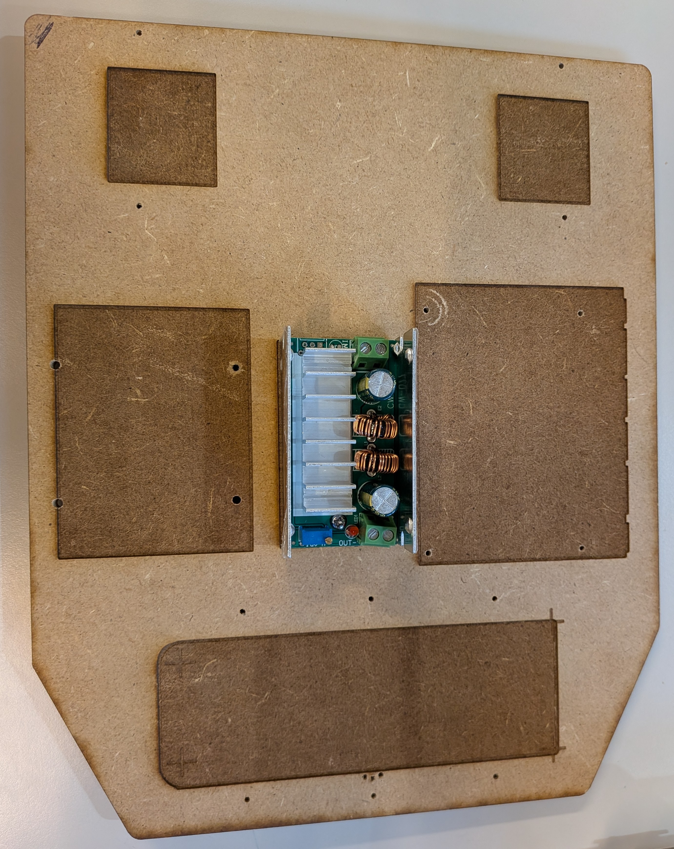
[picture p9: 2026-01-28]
images/Montage/regulateur de tension.jpg

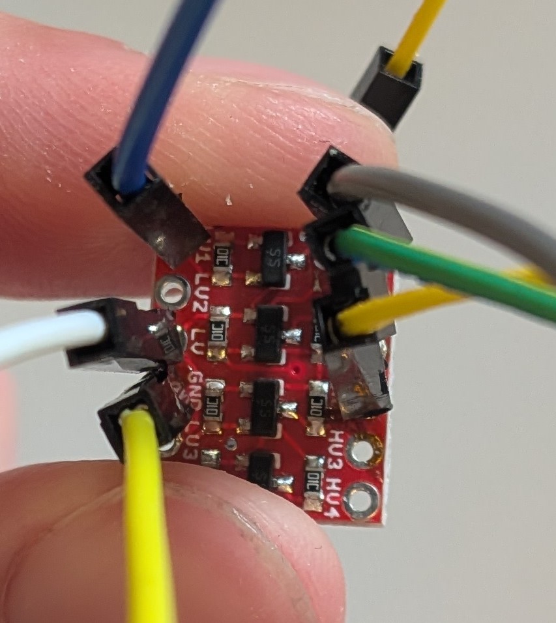
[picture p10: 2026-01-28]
images/Montage/level shifter.jpg

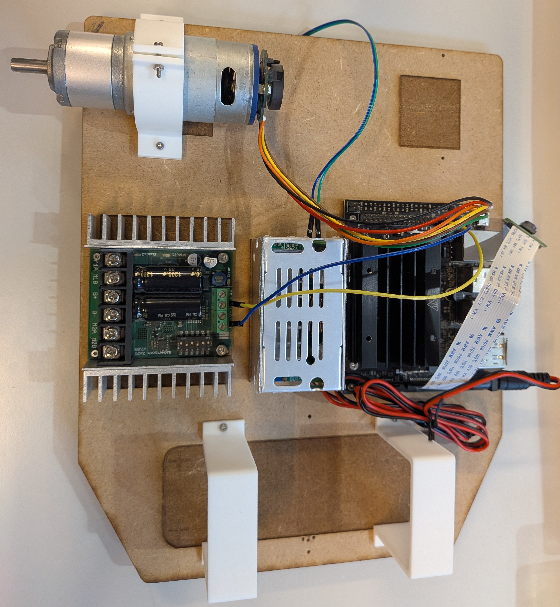
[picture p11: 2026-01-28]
images/Montage/moteur B.jpg

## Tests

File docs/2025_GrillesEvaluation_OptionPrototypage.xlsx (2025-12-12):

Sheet: Soutenance et Prototype
Grille évaluation Option Prototypage - Soutenance et Prototype
NOM - Prénom :
Evaluateurs :
Critères | 5 pts | 4 pts | 2 pts | 1 pt | Coeff | Score
Qualité du prototype | Le prototype est fonctionnel dans son ensemble | Seule la fonctione essentielle du prototype est opérationnelle | Le prototype est non fonctionnel | Il n'y a pas de prototype | 5 |  | 0
Démarche d’ingénierie | Identification des contraintes, validation technique, choix technologiques justifiés. Tests, ajustements, retour sur expérience, résolution de problèmes. | Démarche simple | Des écarts mineurs | Pas de démarche | 5 |  | 0
Management de projet | Mise en place d'outils et méthodes de gestion de projet pertinent et efficace | Quelques outils mis en place mais pas toujours suivi | Pas d'outils mis en place | Aucunes méthodes, le projet n'est pas suivi mais subit | 4 |  | 0
Programmation informatique | La programmation est pertinente et apporte un réel intérêt. La programmation est fonctionnelle La programmation est réfléchit et optimisée | La programmation est fonctionnelle La programmation reste basique | La programmation n'est pas maîtirisée | Pas de programmation | 2 |  | 0
Modélisation 3D | La conception 3D est pertinente et apporte un vrai intérêt fonctionnel | Modélisation esthétique | La conception 3D n'est pas originale Récupération de modèle existant et modifications mineures. | Pas de modélisation 3D | 2 |  | 0
Gestion budgétaire | L'ensemble des coûts du projet sont identifiés : - coût matériel du prototype final - coût matériel des différentes itérations - Coût des pièces non exploitées - Temps de développement | Certains coûts ne sont pas présentés | Des écarts mineurs | Des écarts importants | 2 |  | 0
Réparabilité | Une réflexion sur la fin de vie du produit est proposée. Le choix des matériaux est réfléchi Les commandes de matériel ont été réfléchies Le projet est démontable / réparable facilement. | Pas de réflexion sur la fin de vie. Les commandes de matériel n'ont pas été pertinentes | Démarche faible - prototype non réparable | Pas de démarche | 2 |  | 0
Maitrise et rigueur technique | L'étudiant démontre une maitrise de l'ensemble des technologies mises en œuvre | L'étudiant démontre une maîtrise partielle | L'étudiants ne maîtrise pas les éléments non essentiel à son projet | Aucune maîtrise | 2 |  | 0
Présentation | Structure, clarté, langage technique, gestion du temps. Support de qualité professionnelle Présentation Dynamique | Quelques fautes dans le support Présentation manquant de dynamisme | Plus de 5 fautes dans le support Manque de préparation | Soutenance non préparée | 2 |  | 0
Moyenne |  |  |  |  | 26 | 0 | 0
Evaluation
Commentaires

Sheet: Rapport
Grille évaluation Option Prototypage - Rapport
NOM - Prénom : | 0
Evaluateurs :
Critères | 5 pts | 4 pts | 2 pts | 1 pt | Coeff | Score
Cahier des charges et analyse fonctionnelle | Cahier des charges complet, clair, structuré. Analyse fonctionnelle détaillée et justifiée. | CDC clair et cohérent, analyse fonctionnelle correcte mais partielle. | CDC incomplet ou peu structuré. Analyse fonctionnelle superficielle. | CDC très incomplet ou absent. Analyse fonctionnelle erronée. | 4 |  | 0
Dossier technique – Étapes de réalisation | Étapes complètes et précises (modélisation, fabrication, tests). Visuels professionnels. Archives complètes | Bon niveau de détail, quelques étapes moins documentées. | Documentation insuffisante ou non chronologique. | Documentation très faible ou inexistante. | 4 |  | 0
Tracé des choix techniques | Justification détaillée, alternatives étudiées, cohérence avec CDC. | Justification correcte mais partielle. | Justifications superficielles ou techniques peu adaptées. | Aucune justification des choix. | 2 |  | 0
Management de projet et outils | Usage complet d’outils (Kanban, budget, risques, MVP…). Analyse critique. | Outils utilisés mais analyse limitée. | Usage minimal ou irrégulier. | Absence d’outils de gestion. | 4 |  | 0
Cohérence objectifs / résultats | Alignement parfait + analyse claire des écarts. | Bonne cohérence générale. | Plusieurs incohérences non justifiées. | Manque de cohérence global. | 2 |  | 0
Qualité professionnelle du document | Document structuré, soigné, sans fautes. Mise en page pro. | Document clair, quelques erreurs mineures. | Document brouillon ou peu structuré. | Document difficile à lire, fautes majeures. | 2 |  | 0
Analyse réflexive | Analyse approfondie des réussites, difficultés, améliorations. | Bonne analyse mais moins approfondie. | Analyse superficielle, descriptive. | Aucune analyse réflexive. | 2 |  | 0
Moyenne |  |  |  |  | 20 | 0 | 0
Evaluation
Commentaires

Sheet: Implication
Grille évaluation Option Prototypage - Implication
NOM - Prénom : | 0
Evaluateurs :
Critères | 5 pts | 4 pts | 2 pts | 1 pt | Coeff | Score
Implication et engagement personnel | Très fort investissement : initiative, motivation constante, travail approfondi. | Engagement sérieux et régulier, bonne autonomie. | Engagement variable, travail minimal ou irrégulier. | Faible engagement, travail insuffisant. | 2 |  | 0
Assiduité et ponctualité | Présence irréprochable, aucune absence injustifiée, ponctualité constante. | Bonne assiduité, quelques retards ou absences mineures. (Absences justifiées ou moins de 4 retards) | Assiduité irrégulière, retards répétés ou absences non justifiées. (5 retards) | Absences fréquentes, participation insuffisante. (6 retards) | 2 |  | 0
Respect des échéances | Toutes les échéances respectées ou rendues en avance, travail complet. | Majorité des échéances respectées, retards mineurs. | Plusieurs livrables en retard ou incomplets. | Livrables très en retard ou non rendus. | 2 |  | 0
Professionnalisme (autonomie, rigueur, attitude) | Travail rigoureux, autonomie élevée, attitude professionnelle constante. | Travail sérieux et rigoureux, autonomie satisfaisante. | Manque de rigueur ou autonomie irrégulière. | Attitude non professionnelle, manque de sérieux. | 2 |  | 0
Communication | Communication proactive et régulière, questions pertinentes. | Communication claire et conforme aux attentes. | Communication limitée ou tardive. | Communication absente, ne rend pas compte du travail. | 2 |  | 0
Moyenne |  |  |  |  | 10 | 0 | 0
Evaluation
Commentaires

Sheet: Synthèse Scholaris
Grille évaluation Option Prototypage - Implication
NOM - Prénom : | 0
Evaluateurs :
UE Option | Note
Option : Compétences
Option : Réalisation
Option : Evaluation par les pairs

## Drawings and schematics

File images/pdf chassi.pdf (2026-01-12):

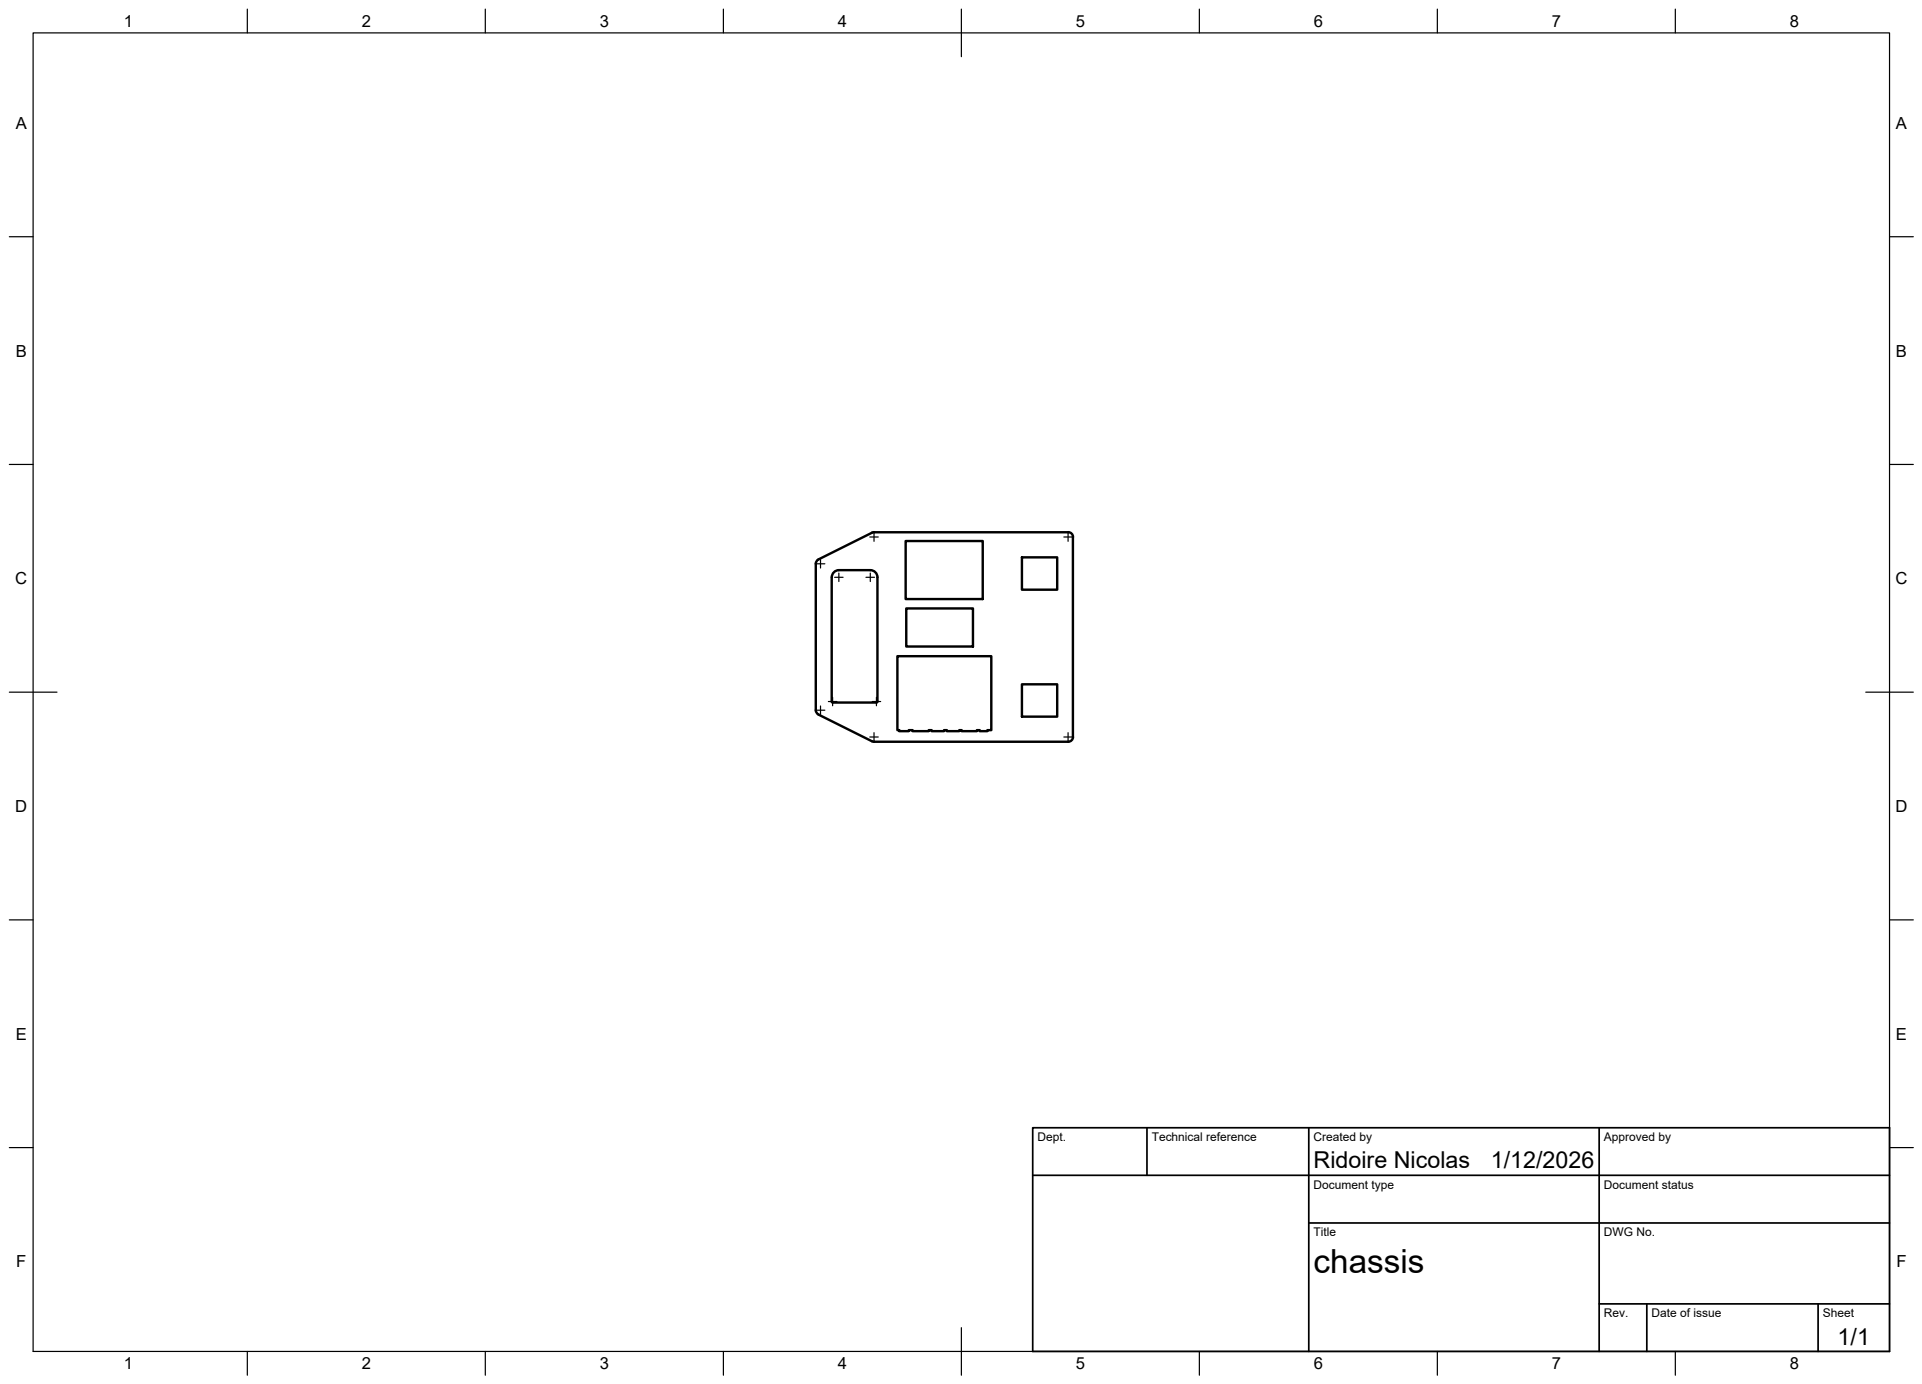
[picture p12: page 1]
Title; DWG No.; Rev.; Date of issue; Sheet

Dept. | Technical reference | Created by Ridoire Nicolas 1/12/2026 | Approved by

Document type | Document status

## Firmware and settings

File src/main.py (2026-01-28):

from flask import Flask, request, Response, jsonify
import globalVar
from command import execCommand
from camera import generateFrames
from os import chdir

chdir("/home/nano/nanocar/src/")
app = Flask(__name__)

automode = False

@app.route("/")
def home():
    content = "Page not found"
    with open('./page/home.html') as file:
        content = file.read()
    return content

@app.route('/videoFeed')
def videoFeed():
    return Response(generateFrames(), mimetype='multipart/x-mixed-replace; boundary=frame')

@app.route("/command", methods=["POST"])
def command():
    action: str = request.get_json()['action']
    print(action)
    execCommand(action)
    return "";

@app.route("/hello")
def helloWorld():
    return "<p>Hello World!</p>"

@app.route("/currentSpeed")
def getCurrentSpeed():
    return jsonify({'speed': globalVar.speed})

if __name__ == "__main__":
    app.run(host="10.42.0.1", port=3000, threaded=True)

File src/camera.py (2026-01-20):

import jetson_inference
import jetson_utils
import cv2
import globalVar
import threading
from command import execCommand

class CameraStream:
    def __init__(self):
        self.stream = cv2.VideoCapture(
            "nvarguscamerasrc sensor-mode=4 ! "
            "nvvidconv ! "
            "video/x-raw, width=1280, height=720, format=BGRx ! "
            "videoconvert ! "
            "video/x-raw, format=BGR ! appsink max-buffers=1 drop=true",
            cv2.CAP_GSTREAMER
        )
        self.grabbed, self.frame = self.stream.read()

    def start(self):
        threading.Thread(target=self.update, args=()).start()
        return self

    def update(self):
        while True:
            (grabbed, frame) = self.stream.read()
            if grabbed:
                self.frame = frame

    def read(self):
        return self.frame

cam = CameraStream().start()

# --- CONFIGURATION GPU ---
# On charge le réseau de neurones sur le GPU (SSD MobileNet V2)
# threshold=0.5 signifie qu'on veut être sûr à 50% que c'est bien une personne
net = jetson_inference.detectNet("ssd-mobilenet-v2", threshold=0.60)

# --- CONFIGURATION ROBOT ---
FRAME_WIDTH = 1280
CENTER_X = FRAME_WIDTH // 2
DEAD_ZONE_X = 250
TARGET_AREA = 400000
AREA_TOLERANCE = 40000

def generateFrames():
    while True:
        frame = cam.read()
        if frame is not None:
            if globalVar.automode:
                frame = followTarget(frame)
            ret, buffer = cv2.imencode('.jpg', frame)
            frame = buffer.tobytes()
            yield (b'--frame\r\n' +
                   b'Content-Type: image/jpeg\r\n\r\n' + frame + b'\r\n')

def followTarget(frame):
    # 1. Conversion OpenCV (Numpy) -> CUDA (GPU)
    # OpenCV utilise BGR, Jetson Inference préfère RGBA
    img_cuda = jetson_utils.cudaFromNumpy(frame)

    # 2. DÉTECTION GPU (C'est ici que la magie opère)
    detections = net.Detect(img_cuda)

    target = None
    obstacle = []

    for d in detections:
        if d.ClassID == globalVar.target_class_id:
            if target is None or d.Area > target.Area:
                target = d
        else:
            obstacle.append(d)
            obs_x = d.Center[0]
            
            # Si l'obstacle est au milieu de l'écran (+/- 300px)
            if (CENTER_X - 300) < obs_x < (CENTER_X + 300):
                # Récupération du nom de l'obstacle pour affichage
                obs_name = net.GetClassDesc(d.ClassID)
                status_text = f"DODGE: {obs_name}"
                
                # Dessin Obstacle (Rouge)
                l, t, r, b = int(d.Left), int(d.Top), int(d.Right), int(d.Bottom)
                cv2.rectangle(frame, (l, t), (r, b), (0, 0, 255), 3)
                cv2.putText(frame, f"{obs_name}", (l, t), cv2.FONT_HERSHEY_SIMPLEX, 1, (0, 0, 0), 2)
                
                ## Esquive
                #if obs_x > CENTER_X:
                #    command = "LEFT"
                #else:
                #    command = "RIGHT"
                #    
                #execCommand(command)
                #cv2.putText(frame, f"{status_text} -> {command}", (20, 50), cv2.FONT_HERSHEY_SIMPLEX, 1, (0, 0, 255), 2)

    # Si pas de personne trouvée
    if target is None:
        cv2.putText(frame, "RECHERCHE CIBLE...", (20, 50), cv2.FONT_HERSHEY_SIMPLEX, 1, (0,0,255), 2)
        if globalVar.search:
            execCommand("RIGHT")
        else:
            execCommand("STOP")
        return frame

    # --- SI PERSONNE TROUVÉE ---
    
    # Récupération des coordonnées
    # L'objet 'd' contient directement le Centre et l'Aire !
    x, y = int(target.Center[0]), int(target.Center[1])
    w, h = int(target.Width), int(target.Height)
    area = w * h
    
    # Dessin sur l'image (Retour visuel)
    # On dessine le rectangle autour de la personne
    left, top = int(target.Left), int(target.Top)
    right, bottom = int(target.Right), int(target.Bottom)
    cv2.rectangle(frame, (left, top), (right, bottom), (0, 255, 0), 2)
    cv2.putText(frame, f"{net.GetClassDesc(target.ClassID)}", (left, top), cv2.FONT_HERSHEY_SIMPLEX, 1, (0, 0, 0), 2)
    cv2.circle(frame, (x, y), 5, (0, 0, 255), -1)
    
    # --- LOGIQUE DE PILOTAGE ---
    # Gestion Direction
    command = "STOP"
    if x < (CENTER_X - DEAD_ZONE_X):
        command = "LEFT"
    elif x > (CENTER_X + DEAD_ZONE_X):
        command = "RIGHT"
    else:
        # Gestion Distance
        if area < (TARGET_AREA - AREA_TOLERANCE):
            command = "FORWARD"
        elif area > (TARGET_AREA + AREA_TOLERANCE):
            command = "BACKWARD"
    execCommand(command)

    # Affichage Infos
    cv2.putText(frame, f"{command} (Conf: {int(target.Confidence*100)}%)", (20, 50), cv2.FONT_HERSHEY_SIMPLEX, 1, (0, 255, 0), 2)

    return frame

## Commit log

2025-12-09 start du cahier des charges + liste commande
2025-12-10 liste de materiel
2025-12-12 cahier des charges fini
    [2025_GrillesEvaluation_OptionPrototypage.xlsx]
2025-12-12 liste de matériel / commandes
2025-12-15 update readme + CAD
    [DC Motor.FCStd, Driver.FCStd, LiPo.FCStd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]
2025-12-17 more doc on the setup + update materials
2025-12-18 no match case, python version on the nano is too old
2025-12-18 add camera feed to the page
2025-12-18 try camera fix
2025-12-18 trying to fix camera
    [camera.py]
2025-12-18 finally working camera feed
2025-12-18 reduce camera quality cause too much latency
    [camera.py]
2025-12-19 test control motor driver
2026-01-12 new CAD
    [Camera.f3d, DC Motor.FCStd, Driver.FCStd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]
2026-01-14 update todo + more CAD files
    [Nanocar assemblage.f3z, Support batterie.stl, roue avant.f3d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]
2026-01-16 use jetson_inference instead of opencv
2026-01-16 add obstacle dodging capacities + speed control in automatic mode
2026-02-22 add user and technical doc
    [listMatériel.xlsx]
